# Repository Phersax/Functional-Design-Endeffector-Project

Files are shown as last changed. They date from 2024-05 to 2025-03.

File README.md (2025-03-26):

# Robotic Grippers Comparative Analysis  




## Project Overview  
This study aims to conduct a comparative analysis between two types of grippers used in robotic manipulation: a 3-finger parallel gripper and a 3-finger adaptive gripper. The research will begin with a description of the development of the parallel gripper and will continue with the design of an adaptive phalanx that will convert the developed parallel gripper into an adaptive gripper. Additionally, the analysis will include a thorough evaluation of the performance of both devices, with particular emphasis on their manipulation capabilities.
The 3D modeling will be carried out using SolidWorks software.

Open-source comparison of two robotic gripper designs:  
- 3-Finger Parallel Gripper  
- 3-Finger Adaptive Gripper (convertible from parallel version)  

Designed for academic research and DIY robotics enthusiasts.  

## Assembly
<p align="center">
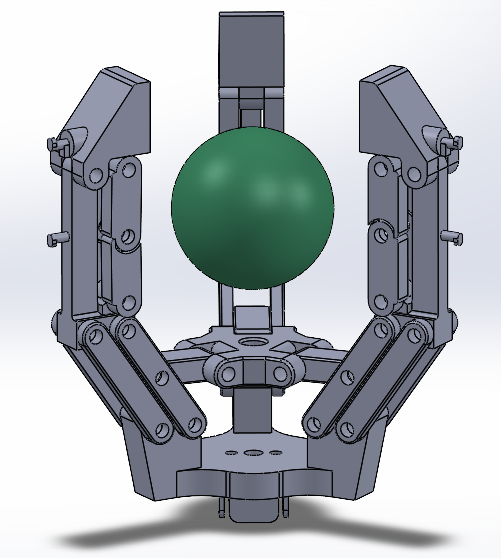
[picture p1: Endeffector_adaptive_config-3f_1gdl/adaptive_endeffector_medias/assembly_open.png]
  
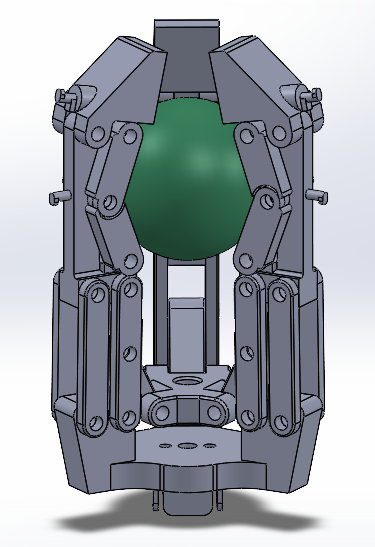
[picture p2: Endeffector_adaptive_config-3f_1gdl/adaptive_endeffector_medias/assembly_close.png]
  
</p>

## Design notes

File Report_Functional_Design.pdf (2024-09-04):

## POLITECNICO DI BARI

DIPARTIMENTO DI INGEGNERIA ELETTRICA E DELL’INFORMAZIONE

LAUREA MAGISTRALE IN INGEGNERIA DELL’AUTOMAZIONE

## Applied Mechanics - Functional Design

## Prof. Ing. Massimo Maria Foglia

# Title:

## Transition from Parallel Gripper to Adaptive Gripper: Design and 3D Simulations

## Students: Francesco Di Chio Nicola Saltarelli Francesco Stasi

ANNO ACCADEMICO 2023-2024

Abstract

This study aims to conduct a comparative analysis between two types of grippers used in robotic manipulation: a 3-finger parallel gripper and a 3-finger adaptive gripper. The research will begin with a description of the development of the parallel gripper and will continue with the design of an adaptive phalanx that will convert the developed parallel gripper into an adaptive gripper. Additionally, the analysis will include a thorough evaluation of the performance of both devices, with particular emphasis on their manipulation capabilities.
Through a series of experimental tests, the performance of the two grippers will be examined in different operational contexts to provide a detailed analysis of their features and advantages. The objective is to provide an in-depth understanding of the performance differences between the two devices.
The 3D modeling will be carried out using SolidWorks software. This process will be documented in the report to ensure a clear understanding of the model development process and the methodologies employed.

CONTENTS

## Contents

Introduction | 1
1 Robotic grippers | 2
2 Parallel gripper design | 6
3 Adaptive finger design | 15
4 Experimental Results | 20
Conclusion | 28
References | 29

CONTENTS

## Introduction

Human labour has always been associated with the acquisition of specific skills, methods, and tools making the work and its environment easier and more effective. Increasing competition from industrial robots for tasks normally carried out by human hands has led to the need for more effective handling equipment, especially prehension tools (more commonly called “grippers”). However, industrial robots are not simply a substitute for people. Their relevance is more often in applications beyond the normal ability (physical or temporal) of conventional manpower. Examples include dirty, hazardous and repetitive work. Just as human hands are the organs of human manipulation, so are robot grippers usually the only parts in direct contact with the workpiece.

Among the wide types of end-effectors, grippers are largely used thanks to their relative simplicity and efficiency in part-handling applications and grasping any physical object, according to the design of the gripper, that can be also manipulated by human hands.

These are the main reasons behind the project, focused on the complete design of two grippers. Starting from the parallel configuration, an adaptive gripper based on the parallel one will be implemented, showing the process of switching from one configuration to another and benefits.

The paper shows all the most important characteristics and steps done in order to develop the grippers.
After a brief introduction and the various classifications that can be made on the robotic grippers, the parallel gripper’s design process will be presented, showing the base mechanism of the gripper, the fingers displacement and the degree of freedom analysis and the design of all parts of the gripper, realized using the SolidWorks software.
The report therefore focuses on the transition to adaptive configuration, showing the new custom parts developed and the main choices made regarding the DC motor and the linear springs to be used.
These choices are important because they have a very close consequence on the operation of the gripper and on the simulation and experimental results obtained in SolidWorks, on which the successive part of the report is focused.
The last part of the papers aims to analyse the results from the SolidWorks simulations, showing advantages and disadvantages of using the two different configurations in terms of applied forces variations, adaptability and forces distribution.

1 ROBOTIC GRIPPERS

## 1 Robotic grippers

A robotic gripper is an essential component of a robotic manipulator. It serves as the robot’s hand and allows the robot to manipulate objects. Recently robotic gripper is widely used for different tasks in various fields. Variety of robotic grippers is developed in high flexibility and multi-function. This project is aimed to study current existing robotic grippers, focusing on the distinction between adaptive grippers and parallel grippers, using a model with three fingers and two phalanges.

### 1.1 Classification

The wide range of shape, size and weight of objects to be manipulated in a production process led to designing of a various types of grippers, that has to be properly selected for a specific task. Therefore is important to distinguish and knowing the grippers types in order to do the correct choice when needed.

### 1.1.1 Configuration-based classification

According to their configuration, grippers can be distinguished in terms of:

- number of fingers : the base configuration of a gripper needs two fingers, sufficient to do the majority of production and manipulating tasks, such as assembly or pick and place. By incrementing the number of fingers one can achieve configurations with multiple fingers for more accuracy and precision in grasping sensitive and fragile objects.

Figure 1: Adaptive three-fingered gripper.

- shape of gripper : grain-filled flexible ball grippers and bellow grippers works changing the shape of the end effector in real time changing the amount of air in the balloon that, in this case, rappresents the gripper. These grippers are also called “Air-Hand” grippers.

### 1.1.2 Actuation-based classification

From the actuation point of view, grippers can be divided in terms of:

- Mechanical actuation : mechanical fingers, that are integral part of the mechanism, are actuated by the main mechanism to grasp objects.
- Cable-driven or sensory feedback actuation : This type of gripper is equipped with a lot of sensors for control purposes. In this type of gripper the design of the robotic arm and the end effector has to be done in order to match with wiring requirements.
- Vacuum grippers : the high level of flexibility of this gripper, while providing a good grip of an object, is due to the use of a rubber or foam suction part to hold the object.

1 ROBOTIC GRIPPERS

Figure 2: Mechanical gripper.

- Hydraulic actuation : using hydraulic pumps one can produce more grasping force compared to other actuations. The disadvantage of hydraulic grippers is that they need constant maintenance.
- Pneumatic actuation : the fingers movement and displacement is made by changing the air pressure in the valve. Small dimensions and low weight are key factors to pay attention to when this type of gripper is used.
- Servo-electric actuation : Using servo-motors used to control the fingers ensures high flexibility and low maintenance costs.
- Magnetic actuation : Making use of the principles of magnetism, these are used for holding ferrous objects.

### 1.1.3 Stiffness-based classification

This important classification in based on the material’s stiffness. In particular the main division is relative to:

- Rigid grippers : these are the traditional ones and they are largely used in industrial applications, in which high precision and less flexibility of fingers is required.
- Soft grippers : the fingers are made by flexible material, allowing to grasp object with very different shapes. These types of grippers and robots are currently important areas of interest for scientists and engineers, especially for medical applications. Grain-filled flexible ball grippers and bellow grippers belongs to soft robots, such as the universal grippers.

Figure 3: Soft gripper.

1 ROBOTIC GRIPPERS

### 1.1.4 Application-based classification

Grippers are not only used in industrial applications, but they also works in:

- Surgical application : especially for Minimally Invasive Surgery (MIS), small grippers and soft grippers are the main choice.
- Assistive application : there are a lot of grippers designed for people with disabilities or, for example, mounted on Unmanned Aerial Vehicle (UAV).
- Research application : a big area of interest is also linked to underwater or underground researches.

### 1.2 Case study

As previously mentioned, the primary objective of this study is to conduct a comparison between parallel and adaptive grippers. Therefore, this subsection will outline the main differences between these two types of devices to facilitate understanding of the results obtained from this research.

### 1.2.1 Parallel grippers

Due to their simplicity of control and relatively low cost, parallel grippers have been widely utilized as end-effectors in industrial robotic systems. Particularly, parallel grippers with fingers moving along a single linear trajectory are notably easy to use. This is because the position of both fingers relative to the linear trajectory remains consistent and constant throughout. This feature greatly simplifies the control process and ensures precise repeatability of operations.

Figure 4: Gripper with linear guide mechanism (Kobayashi et al., 2019).

The collision free space of the motion of the robot which the gripper is attached to depends on the dimensions of the gripper. When grasping objects with different dimensions is performed using a single gripper, the width of the gripper is determined by the largest dimension of the objects; on the other hand, a gripper with large width is undesirable from the collision free space of the robot motion point of view. Because of this issue, the parallel grippers have been usually utilized for tasks to handle the same or a similar dimensions of objects, not for tasks to handle of objects with different dimensions. Grasping of the same or a similar dimensions of objects can be realized by a compact gripper with a compact linear guide mechanism having short stroke.
(Kobayashi et al., 2019) [4] addresses the issue of parallel grippers using the linear guide mechanism and proposes a new parallel open-close gripper.
The width of the proposed gripper depends on the fingers opening width, that is, the gripper becomes small when it grasps a small object and becomes large when it grasps a large object. The proposed gripper can be applied to tasks handling objects with different dimensions without restricting the collision free motion space.

1 ROBOTIC GRIPPERS

Figure 5: Gripper with parallel four bar mechanism (Kobayashi et al., 2019).

With this mechanism, the gripper can open and close fingers with keeping their orientations constant. Normally, the grasping flat surfaces of fingers are parallel to each other. The width of the gripper with four bar parallel linkage can be designed smaller than its finger stroke.

### 1.2.2 Adaptive grippers

An adaptive mechanical system is one in which some form of intelligence is embedded into the mechanics. In such a system, no sensors or complex controllers are required to perform the main task since the mechanical system itself will provide the required adaptive behavior.
In many robotic applications, the manipulation of objects with very complex mechanical hands is not essential and grasping devices are sufficient. However, simple grippers are not appropriate in most cases because they are not capable of adapting to the shape of different objects.
Hence, the development of versatile robotic hands which are capable of grasping a wide variety of objects with a very simple control structure is of great interest for many applications.
It is clear that robot hands based on the latter principle are adaptive mechanical systems since they can adapt to the shape of the objects simply by the mechanical action of their components. Since this behaviour implies that motion takes place without control actions, underactuation must be introduced.
An underactuated mechanism is one which has fewer actuators than degrees of freedom (dof)s. When applied to mechanical fingers, the concept of underactuation leads to mechanical adaptiveness. Mechanically adaptive fingers envelope the objects to be grasped and automatically adapt to their shape with a limited number of actuators usually one and without complex control strategies. The implementation methods of underactuated mechanisms are generally classified into three types: using tendon [6], linkage mechanism [7], and mechanical elements such as gears [8].Most of the research of the underactuated mechanism is focusing on reducing the control complexity of multi fingered robot hands.

2 PARALLEL GRIPPER DESIGN

## 2 Parallel gripper design

The proposed gripper consists, as shown in the Figure 6, of three identical fingers equally spaced along a circumference, dividing it into three equal parts. The fingers displacement is realized thanks to a quite simple mechanism driven by a single actuator : a small DC motor, having its own screw shaft, moves in a linear way the gripper’s palm connected to it and, thanks to a rods system, this displacement generates the opening and closing fingers’ movement.

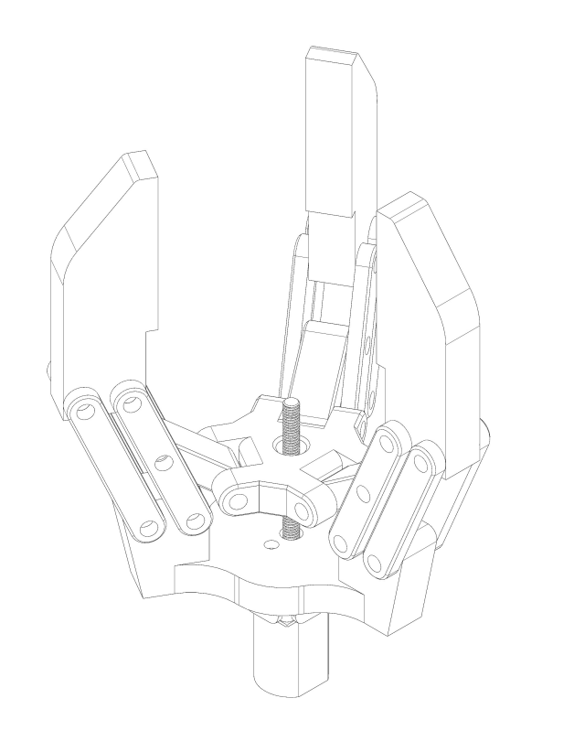
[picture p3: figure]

Figure 6: Model of the three fingers parallel gripper

The proposed solution is especially suitable for the grip of spherical or cylindrical objects, on which the grip is firm and the pressure applied is uniform thanks to the three contact points.
The main advantages that characterize the gripper are in terms of efficiency, ease of implementation and costs thanks to the reduced number of parts.

### 2.1 Degree of freedom analysis

Focusing on a single finger, one can demonstrate that the mechanism allowing the movement is characterized by one degree of freedom. This is an important feature, because it allows a fairly simple study of the kinematic behavior of the entire gripper.

In order to demonstrate this, the Grübler’s formula can be used, which states the number of degrees

2 PARALLEL GRIPPER DESIGN

of freedom of a mechanism can be calculated in the following way:

dof = m(N − 1 − J) +X

J

i=1

fi | (1)

where:

- dof : degrees of freedom of the mechanism;
- m : equal to 6 for spatial bodies, 3 for planar;
- N : number of bodies, including ground;
- J : number of joints;
- f : degrees of freedom of each joint.

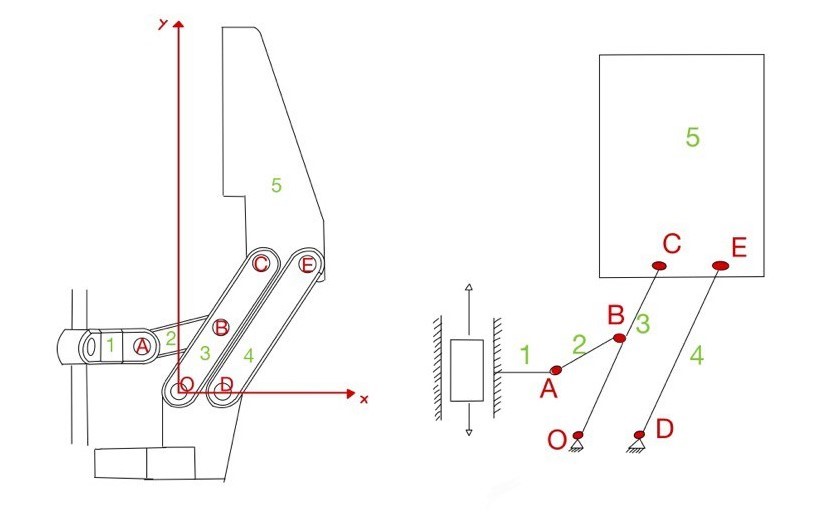
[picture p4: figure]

Figure 7: Constraints analysis

According to the Figure 7, one can see that every finger mechanism is characterized by five bodies (six with the ground), six revolute joints (A,B,C,D,E,O) and one prismatic joint to which the body 1 is subject. In addition, the movement of each finger can be seen as a planar motion.
For this reasons one can stated that m is equal to 3, N is equal 6, J is equal to 7 and the and the sum value is equal to 7 because for every joint there is one degree of freedom.
Applying this values to the Grübler formula one can have:

dof = m(N − 1 − J) +X

J

i=1

fi = 3(6 − 1 − 7) + 7 = 1 | (2)

2 PARALLEL GRIPPER DESIGN

### 2.2 Finger displacement analysis

The chosen approach for studying the kinematic behavior of the finger mechanism makes use of the complex numbers in order to generate the so called closing equation in 2D. Following this method, the mechanism is outlined through vectors expressed as complex numbers, so in terms of magnitude and phase. Using the Euler formula, a non linear system of equations can be obtained and its resolution allows to have a general understanding of the possible displacement of the mechanism.

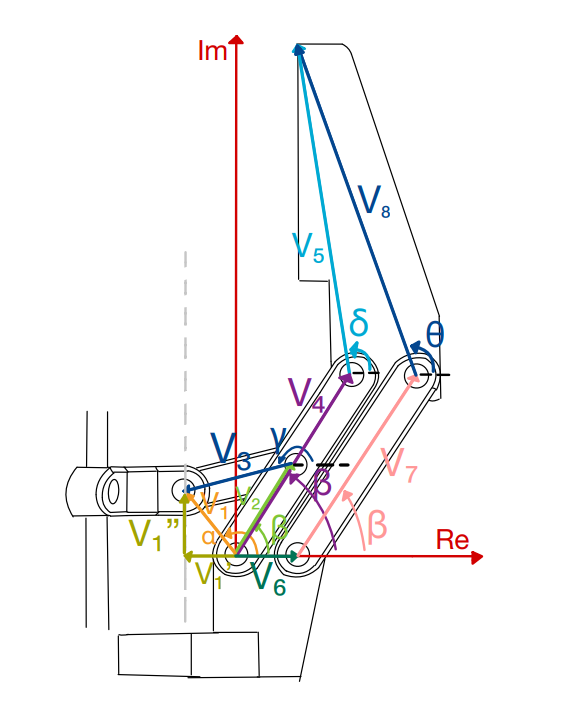
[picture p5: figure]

Figure 8: : Closed kinematic chains

In order to study the mechanism two closing equations have been developed. The first one states that:

V1 − V2 − V3 = 0 | (3)

Expressing the vector V1 as sum of V

′
1

and V

′′
1

the final closing equation is:

V

′
1 + V

′′
1 − V2 − V3 = 0 | (4)

Expressing the equation (4) in terms of amplitude and phase one can obtain :

V

′
1

e

−jπ + V

′′
1

e

j

π
2 − V2e

jβ − V3e
jγ = 0 | (5)

2 PARALLEL GRIPPER DESIGN

Using the Euler formula e

jx = cos(x) + jsin(x) , one can divide the closing equation into two equations, one for the real part and one for the imaginary one. In this way one can obtain a non linear system of two equations in two unknowns, that in this case are the angles β and γ.

The feasible range of variation of V

′′
1 was experimentally deducted from SOLIDWORKS. The range of variation used in Matlab for the non linear system resolution is therefore:

V

′′
1 = [−1.79 : 11.2] | (6)

expressed in mm and referred to the origin.

The same method was used also for the second closing equation :

V4 + V5 − V6 − V7 − V8 = 0 | (7)

Expressing the equation (7) in terms of amplitude and phase one can obtain:

V4e

jβ + V5e

jδ = V6e
j0 + V7e

jβ + V8e
jθ | (8)

After simplifications and using the Euler formula you obtain another non linear system of two equations.

The obtained results are shown in the following figures :

Figure 9: Initial position of the mechanism

2 PARALLEL GRIPPER DESIGN

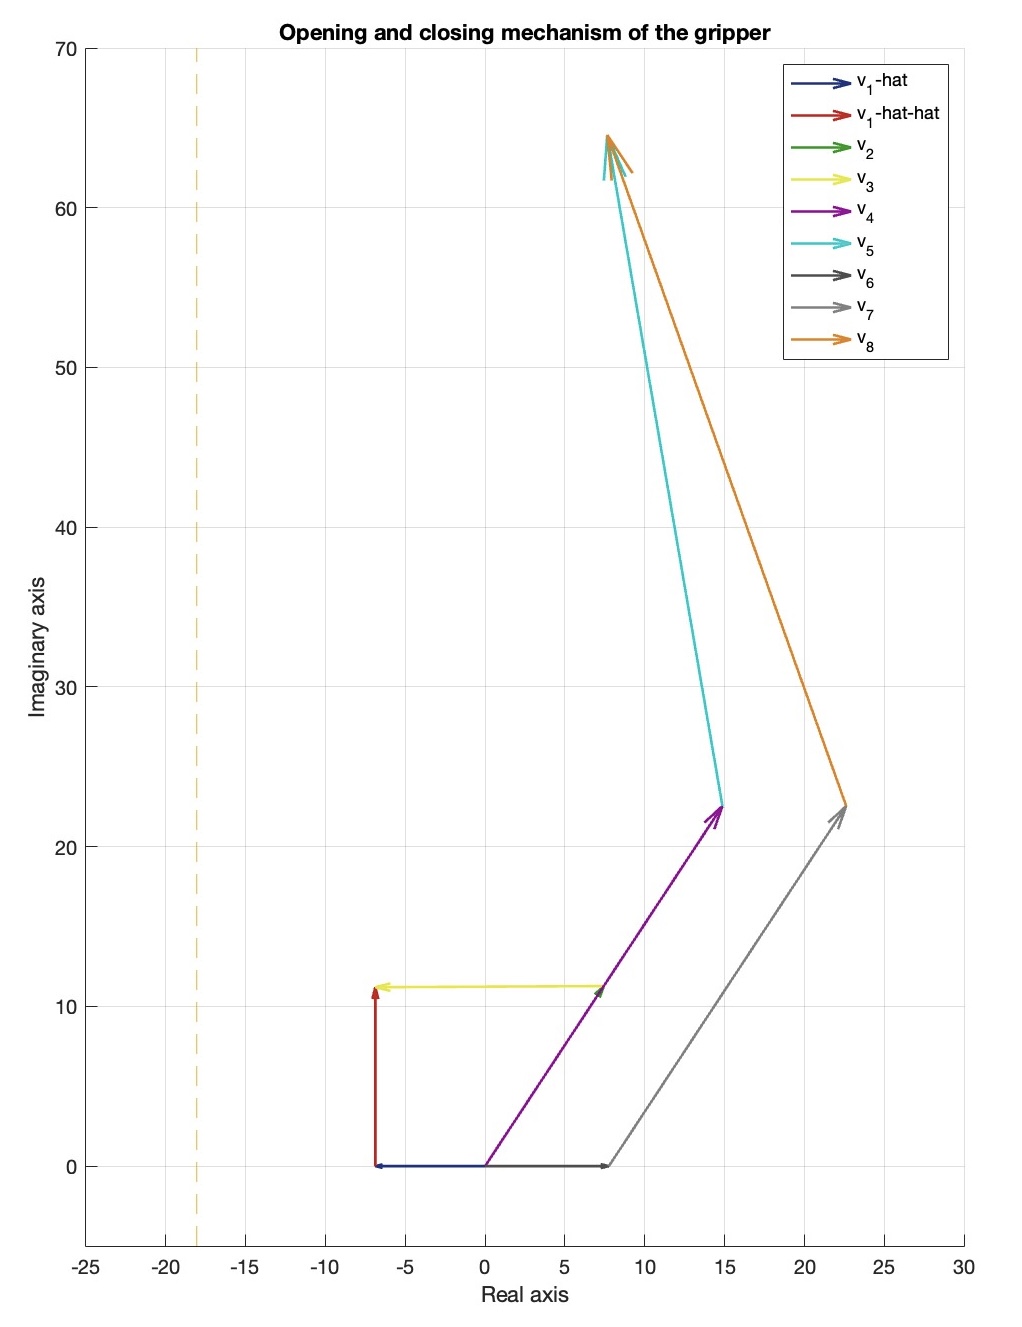
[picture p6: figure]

Figure 10: Final position of the mechanism

### 2.3 SolidWorks 3D model

The 3D model of the designed gripper was developed using SolidWorks, a very powerful software useful also for the contact forces analysis.
The design process started with the creation of fully customized individual parts which were later assembled thought concentricity and coincidence constraints, thus generating the final model.

### 2.3.1 Base part design

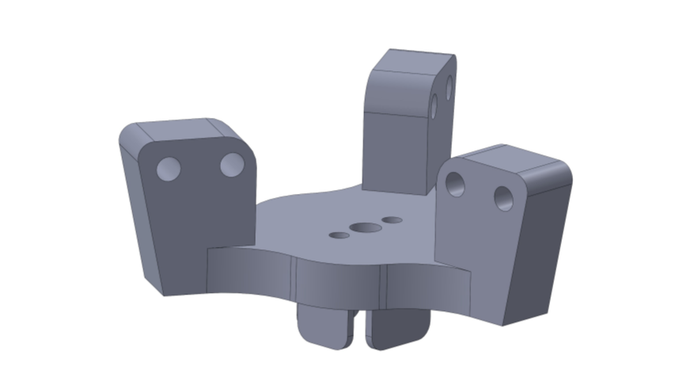
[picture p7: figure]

Figure 11: Base part design

2 PARALLEL GRIPPER DESIGN

The base is mainly composed of a flat main extrusion and three external along the circumference on which there are holes for the connecting rods between the base and the finger. The base is also provided by a central holes and an adapter in the lower part to accommodate the motor and the shaft.

### 2.3.2 DC motor enclosure

The chosen actuator is the 12 GA Miniature DC Gear Motor Screw Shaft. The developed casing ensures a good protection against external agents, increasing the reliability of the gripper.

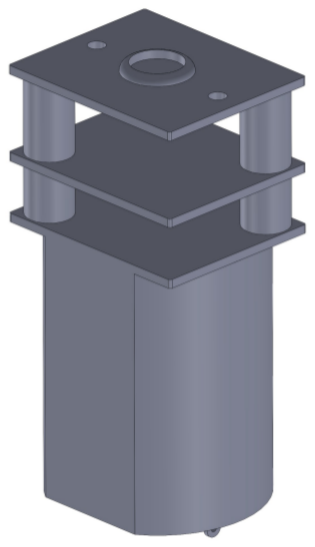
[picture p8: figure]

Figure 12: DC motor enclosure

### 2.3.3 Threaded shaft design

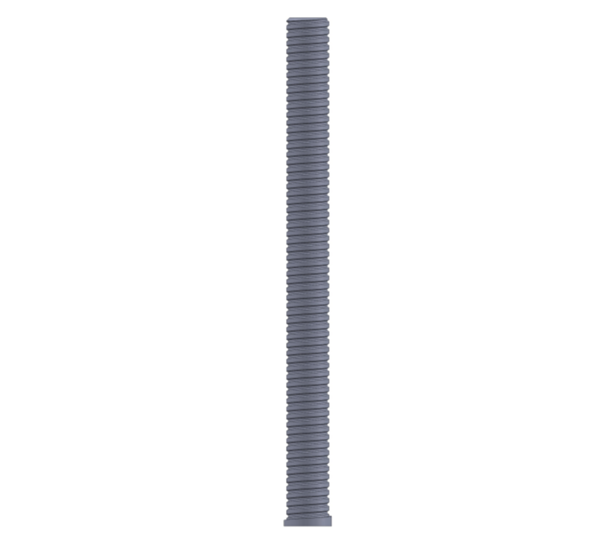
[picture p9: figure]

Figure 13: Threaded shaft

2 PARALLEL GRIPPER DESIGN

The opening and closing fingers movement is possible thanks to a threaded shaft, to which the palm of the gripper is attached, moved by the DC motor. The construction parameters of the shaft are height (32 mm) and pitch (0.5 mm).

### 2.3.4 Palm design

The central element of the gripper mechanism is the fully customized palm. The central hole accommodate the DC motor shaft, while the six external holes generate the revolute joints connecting the palm with the rods.
The design of the palm required much attention in order to have a contact-free slide between the palm and all other parts of the gripper, especially with the base.

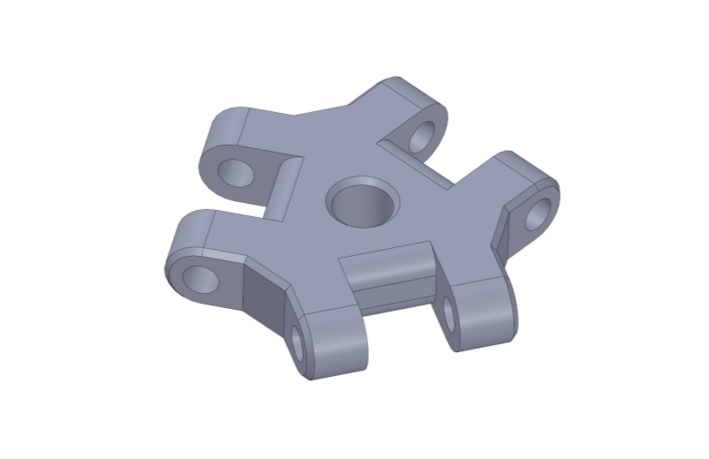
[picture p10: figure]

Figure 14: Gripper palm

### 2.3.5 Connection rods

Three types of rods are used in order to realize the opening and closing finger movement.

The first type of rods makes possible the connection between the base and the finger. In particular, these rods have two holes : one creates the revolute joint with the external hole of the external extrusion of the base, while the second hole generates the external revolute joint on the finger.

The second type of rods is characterized by the same dimensions of the first type rods, but with an additional central hole. The two external holes have the same function of the first type rods ones, while the central one makes the connection with the third type rods.

The third type rods are are shorter and thicker with respect to the other types rods. These rods create a connection between the palm and the central hole’s second type rods.

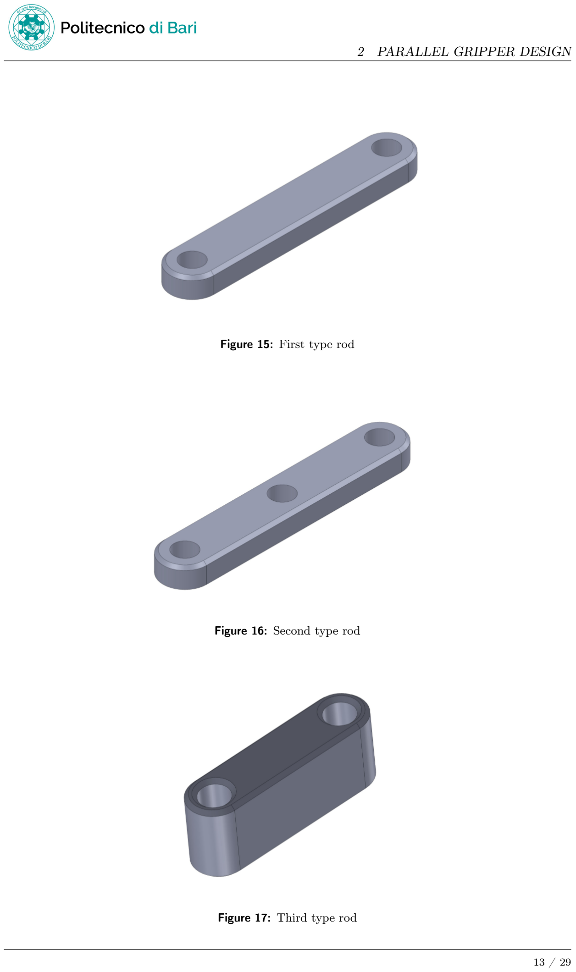
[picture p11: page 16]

2 PARALLEL GRIPPER DESIGN

Figure 15: First type rod

Figure 16: Second type rod

Figure 17: Third type rod

2 PARALLEL GRIPPER DESIGN

### 2.3.6 Finger design

The finger is quite simple single part, obtained with a simple extrusion. You can notice that that flat internal part make contact with the object to be grasped. The flat design allows to grasp spherical object with different size a very solid way.
The holes realize the revolute joint with the first and second type rods.

Figure 18: Gripper finger

3 ADAPTIVE FINGER DESIGN

## 3 Adaptive finger design

To enable the transition from a parallel gripper to an adaptive one, a specific modification was made to the non-adaptive phalanx, avoiding alterations to the entire model. This strategy allowed us to obtain an adaptive gripper simply by modifying the final phalanx of the parallel gripper, while keeping the palm and the opening and closing mechanism unchanged. This approach was chosen with the objective of comparing the two models, as described in the project abstract.

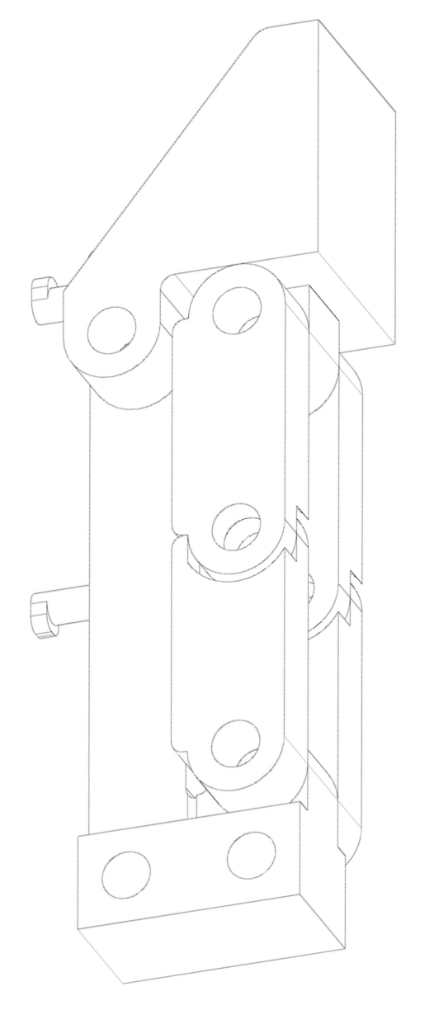
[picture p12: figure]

Figure 19: Adaptive finger’s sketch

For simplicity, in this section we will focus exclusively on describing the adaptive phalanx model of the gripper, as it would be redundant to describe again the base and palm of the gripper. Thanks to this adaptive phalanx, it is now possible to grasp objects by adapting the phalanx to the shape of the object. All of this is made possible through the use of springs.

When the phalanx comes into contact with an object, the four front segments, as depicted in Figure 19, move and conform to the surface of the object, enabling a secure and flexible grip. The springs assist in restoring the phalanx to its original position once the object is released, ensuring that the phalanx always returns to its initial configuration, ready for the next gripping operation.

Utilizing an adaptive phalanx offers numerous advantages:

- Greater Flexibility: The ability to adapt to various shapes and sizes of objects makes the gripper highly versatile.
- Secure Grip: Automatic adaptation to the object’s surface enhances grip stability and security, reducing the risk of slippage.

3 ADAPTIVE FINGER DESIGN

- Simplicity of Design: Using springs for restoring the original position is a simple and effective solution that does not require complex control systems or additional actuators.

These advantages make the adaptive gripper an efficient and versatile solution, significantly enhancing the capabilities for grasping and manipulating objects.

### 3.1 Degree of freedom analysis

In this subsection, the degrees of freedom of the adaptive phalanx will be determined, following the method previously used to analyze the opening and closing mechanism of the parallel gripper. This calculation quantifies the number and nature of independent movements that the adaptive phalanx can perform.

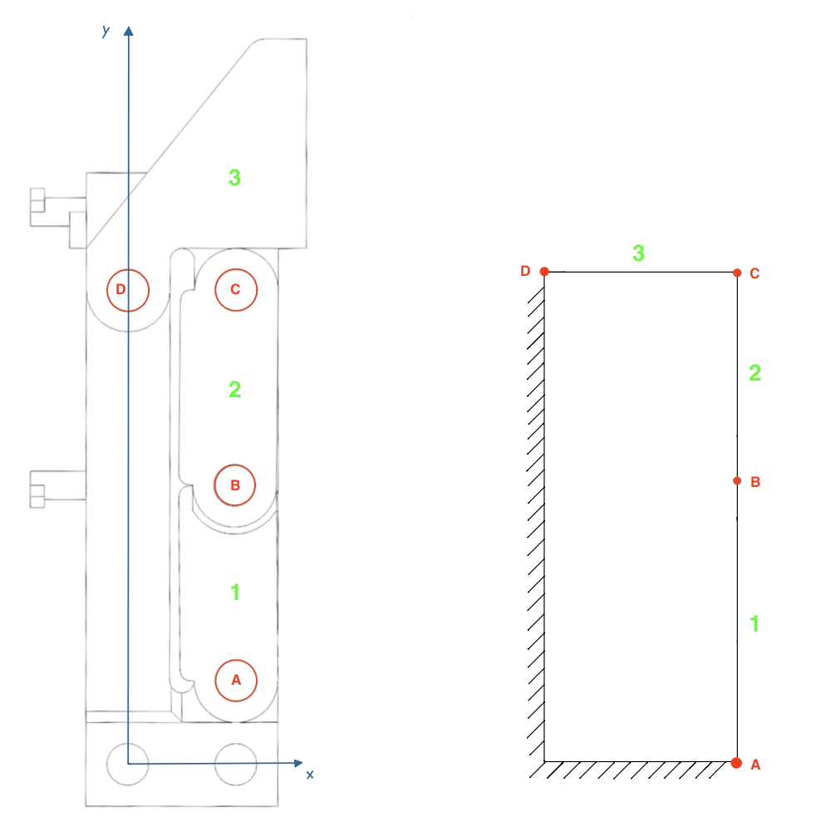
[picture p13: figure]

Figure 20: adaptive finger’s dof analysis

In Figure 20, on the left, a technical side view of the adaptive phalanx is shown, while on the right, a simplified schematic representation facilitates the calculation of its degrees of freedom. The phalanx is equipped with 4 revolute joints and consists of 3 bodies. Therefore, the degrees of freedom of the phalanx are:

dof = m(N − 1 − J) +X

J

i=1

fi = 3(4 − 1 − 4) + 4 = 1 | (9)

3 ADAPTIVE FINGER DESIGN

### 3.2 SolidWorks 3D model

### 3.2.1 Fixed part of the adaptive finger

The fixed part of the adaptive finger in Figure 21 is designed in an L-shape. This part connects the tip of the finger with the bars, which in turn are connected with the base and palm of the end-effector.
The part is designed not to collide with the movable phalanges during closing and opening. A spring attachment is also added, as well as a slide rail (a channel that only allows elongation and compression while preventing it from moving laterally).

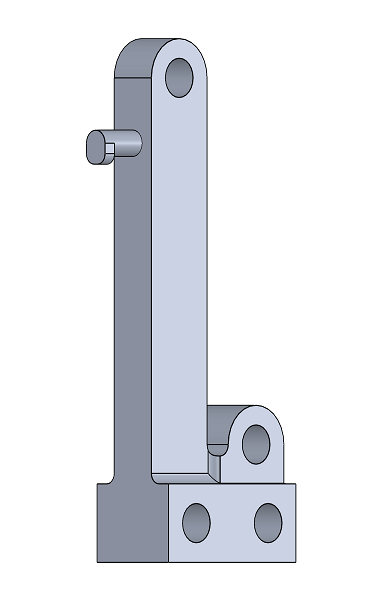
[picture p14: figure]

Figure 21: fixed finger part

### 3.2.2 Mobile phalanges

Phalanges are composed of the same repeated part so that assembly is less complex. In particular, they are made similarly to the connection bars of the static model, but with some tricks to maintain a reduced thickness by modifying the connection between upper and lower phalanges.
In addition, a knocker necessary to prevent reverse rotation of the bars is added. This knocker implies a rotation limitation between the constraints during simulation.
Figure 22 shows the connection between upper and lower phalanges, made with the same repeated part.

3 ADAPTIVE FINGER DESIGN

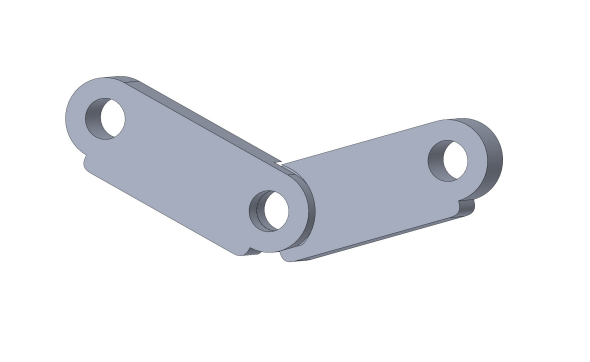
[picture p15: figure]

Figure 22: mobile phalanges parts

### 3.2.3 End part of the finger

The terminal part of the adaptive finger (figure 23) must connect the fixed part with the movable phalanges. Care is taken to avoid creating intersections during movement. The profile is made from the static model of the end-effector. The second hook of the spring is then inserted.

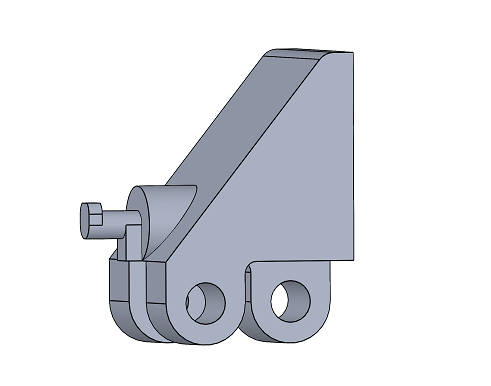
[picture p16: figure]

Figure 23: terminal finger part

3 ADAPTIVE FINGER DESIGN

### 3.2.4 Parts assembly

The finger, which will be directly substituted for the three fingers of the static model, is thus assembled; the spring brings the end-effector to the rest configuration.
Figure 24 shows the finger assembly with a bending test and the addition of the spring for a dynamic study test, while a complete assembly of the new adaptive end-effector can be seen in figure 25.

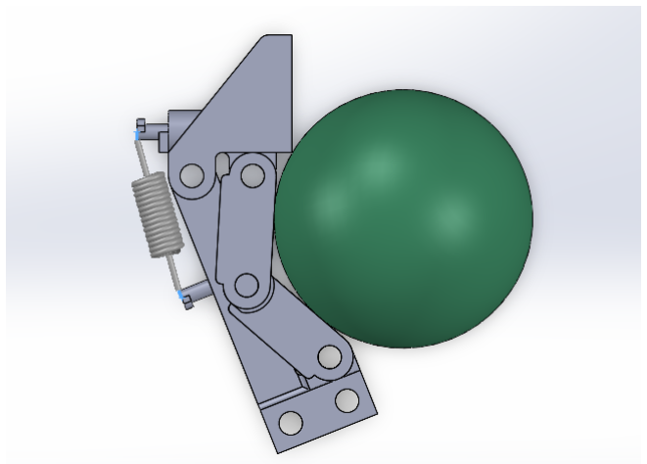
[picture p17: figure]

Figure 24: finger assembly

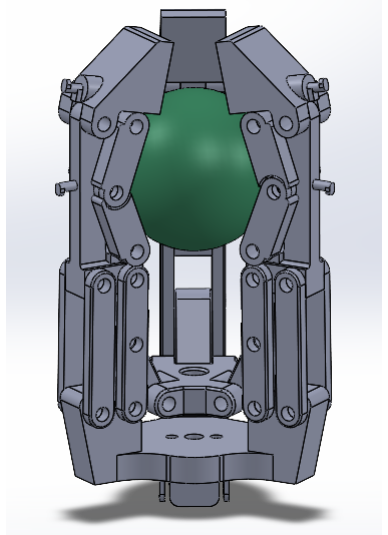
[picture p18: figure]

Figure 25: Complete assembly

4 EXPERIMENTAL RESULTS

## 4 Experimental Results

In this section of the documentation, the results of simulations conducted using Solidworks Motion will be presented. The tests were performed to compare the contact force generated by a gripper in both parallel and adaptive gripper configurations.

The object used for the gripping tests is an aluminum sphere 3.0205 (EN-AW 1200) with a variable diameter. Three spheres of different diameters were employed to analyze how the contact force varies with changes in the diameter and mass of the sphere. Aluminum was selected as the material for the sphere due to its mechanical properties, such as lightness and strength, which make it ideal for simulations aimed at obtaining an accurate and representative response under the given load conditions.
It should be noted that the images presented in this section depict the gripper in a simplified version, excluding the motor and threaded rod necessary for the opening and closing mechanism. In the simulation, the motor’s function, opening and closing the fingers, was replaced by a constant force of 55 N applied to the palm of the gripper, enabling the closing and gripping of the object.

### 4.1 Gripping force calculation

This subsection will demonstrate how to calculate the minimum gripping force required to grasp an object, given the coefficient of friction between the object and the rubber applied to the gripper’s phalanges, as well as the mass of the object itself. The use of rubber pads on the phalanges is particularly beneficial as it enhancing the grip and reducing the risk of the object slipping.

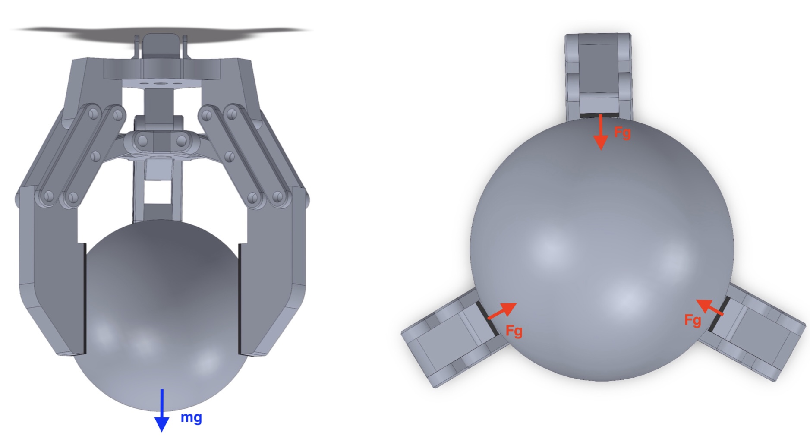
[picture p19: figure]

Figure 26: Parallel gripper in contact with a large sphere.

As shown in Figure 26, the left side displays a front view of the parallel gripper while grasping a sphere, which is the object used for the simulation. On the right side, a bottom view is provided, where the directions of the gripping forces necessary to hold the sphere in place are indicated. Therefore, the gripping force required to grasp the object on each phalange is:

Fg =

mg
µN
∗ S | (10)

4 EXPERIMENTAL RESULTS

where Fg is the gripping force to be applied to each phalange, m is the weight of the object to be grasped, g is the gravitational constant, µ is the coefficient of friction between the materials in contact, N is the number of gripper fingers and S is a safety factor, typically set to 2.

### 4.2 Choice of linear spring

As shown in Figure 24, each finger of the adaptive configuration requires a linear spring that allows the finger to adapt correctly to the object to be grasped, also ensuring the return to the vertical position of the finger when the palm of the gripper is fully raised.
For these reasons the choice of the spring to be used is extremely important, having important consequences for the behaviour and functionality of the gripper.

The chosen spring is a cheaper one, easily available and purchasable on the web, shown in the Figure 27 :

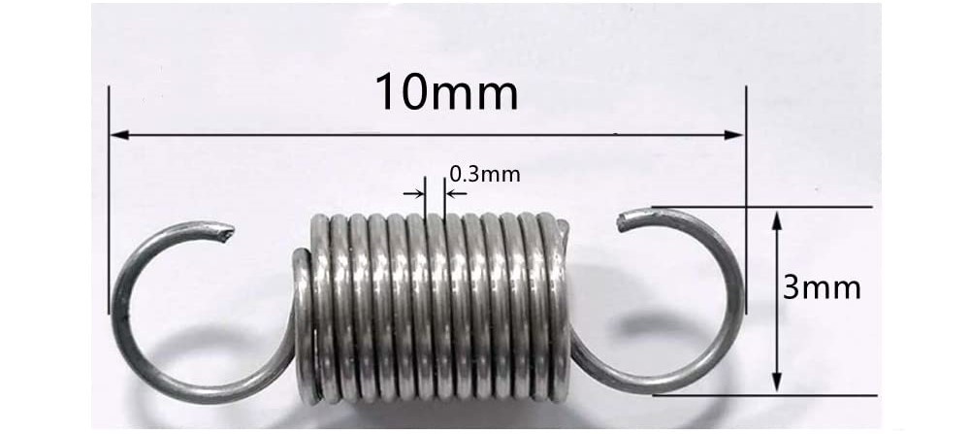
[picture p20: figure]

Figure 27: Linear spring’s parameters

In order to carry out the simulations on Solidworks Motion, the elastic constant and the free length of the spring have to be known.
The free length can be derived from the Figure 27 (10 mm), while the elastic constant is not provided, so is necessary to calculate it.
In order to do it, the following equation [9] can be used :

k =

Gd⁴
8nD³

(11)

where :

- G is the spring material stiffness module ;
- d is diameter of the spring wire ;
- n is the number of active coils ;
- D is the average diameter of the spring.

By taking these parameters from Figure 27 and setting G = 79 GP a, a typical G-value for steel, you obtain, using the Formula 11, that the elastic constant of the spring is equal to 2.9 N/mm.

This result is acceptable and shows that the spring has a good elasticity. As consequence of this, the finger is characterized by a good adaptability to the objects to be grasped, regardless from the

4 EXPERIMENTAL RESULTS

object size. In addition, if the spring constant is too high, the finger will not be able to bend, thus losing its adaptive behaviour.
Summing up, the great adaptability that can be achieved and the availability of the spring makes make this choice in line with the project’s objectives.

### 4.3 Choice of electric DC motor

The choice of motor is crucial since it determines the maximum gripping force applicable by the endeffector and also the closing and opening speed. Among the various types, the DC motor is chosen, which, having a linear torque characteristic, makes it easy to deduce the force that can be obtained from the feed-forward construction parameters, as shown below:

T = K · ϕ · Ia | (12)

The obtained torque T thus depends only on a constant K given by the construction parameters, magnetic flux ϕ and armature current Ia.

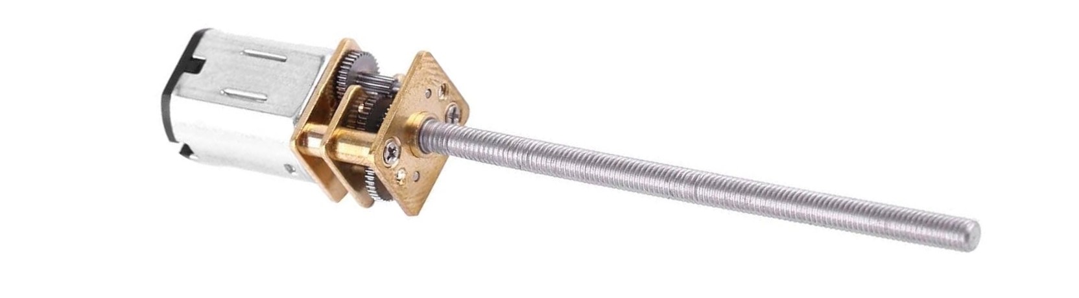
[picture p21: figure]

Figure 28: motor with gearbox

This DC motor must also respect the small size of the system while maintaining a torque capable of making the system functional, even introducing a gearbox to have the right compromise between torque and speed obtained. It is also necessary to transform the rotary motion of our motor into a linear motion suitable for the movement of the palm in our endeffector.
We therefore choose the type of motor shown in Figure 12 that meets the following characteristics, where the M3 threaded rod ensures linear motion.

Then we go on to choose the gearbox to calculate the force of our motor on the palm. Looking at the datasheets of these motors gives indicative tables.
We choose a supply voltage of 6V, with a gearbox that allows a torque at rated load of 4, 903 · 10⁻³Nm and a speed of 100, 531rad/s.
Considering these data, the force transmitted to the palm through the threaded rod can be calculated by the following formula [10]:

F =

2 · π · T · η
P

≈

2 · π · 4, 90 · 10⁻³
- 0.9
0.5 · 10⁻³
≈ 55N | (13)

where :

- F is the resultant force placed on the palm of the endeffector ;
- T is the torque produced by the motor ;
- η is the efficiency set to 0.9 ;
- P is the pitch of the threaded rod equal to 0.5mm for a diameter of 3mm.

4 EXPERIMENTAL RESULTS

In this formula we take into account an efficiency set by us and neglect the friction produced in the movement, however, the value obtained is only indicative of a force that can be used in the simulation phase, this value in fact will always be modifiable by going to check the power parameters of the motor.
To calculate the linear velocity of the palm displacement we can use the following formula where ω is the angular velocity and p is the pitch of the threaded rod. Knowing that the excursion made by the part we can calculate the time taken for the complete opening and closing of the endeffector.
v = ω · p ≈ 50 · 10⁻³mm/s | (14)

### 4.4 Simulations with Large Sphere

In this subsection, the results obtained from the simulation of the parallel and adaptive gripper interacting with a sphere of 26mm radius and approximately 200 g mass will be presented.

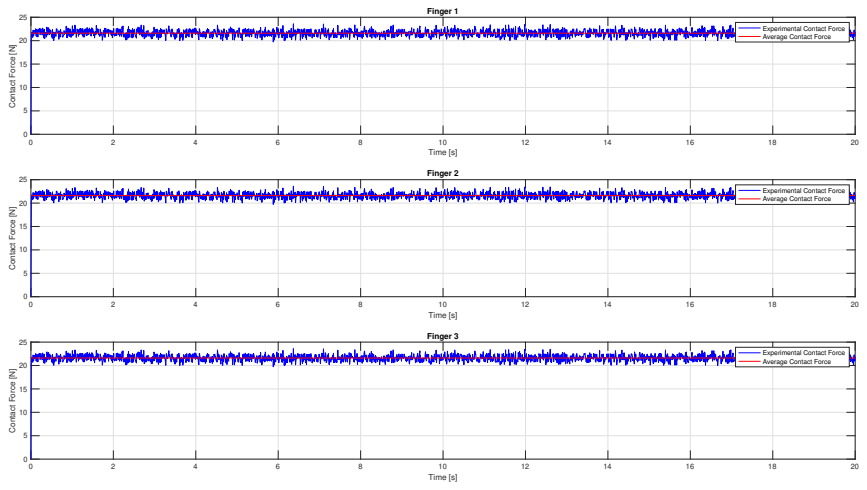
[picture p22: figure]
Time [s]; Contact Force [N]; Finger 1; Experimental Contact Force Average Contact Force; Finger 2; Finger 3

Figure 29: Contact force between the phalanges of the parallel gripper and the sphere.

Figure 29 illustrates the variation in contact force between the phalanges of the parallel gripper and the sphere. It can be observed that the contact force is approximately 22 N, which is higher than the gripping force required to hold the object. Specifically, an aluminum sphere 3.0205 (EN-AW 1200) with a radius of 26 mm has a weight of about 200 g. Given that the static friction coefficient between rubber and aluminum is 0.25, applying Formula 10 yields a gripping force of approximately 5.5 N.

Figure 30 shows the trend of the contact force between the phalanges of the adaptive gripper and the sphere. The graphs highlight that two phalanges per finger come into contact with the sphere. The ’lower phalanx’ refers to the phalanx closest to the palm, while the ’upper phalanx’ is the one situated between the lower phalanx and the outermost phalanx, which is the third and final phalanx of the adaptive finger. It can be observed that once the gripper grasps the object, the contact force is approximately 3.5 N for the lower phalanx and 5.5 N for the upper phalanx.

4 EXPERIMENTAL RESULTS

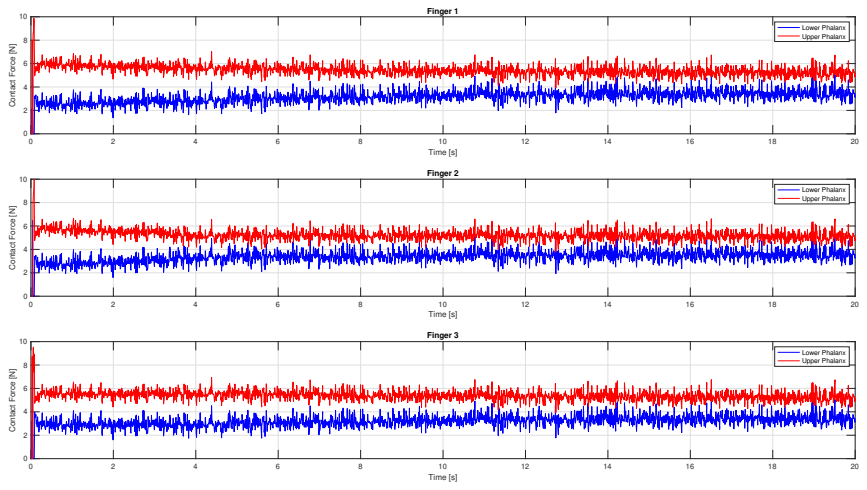
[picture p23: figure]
Time [s]; Contact Force [N]; Finger 1; Lower Phalanx Upper Phalanx; Finger 2; Finger 3

Figure 30: Contact force between the phalanges of the adaptive gripper and the sphere.

### 4.5 Simulations with Medium Sphere

By reducing the size of the sphere to a 22mm radius, we obtain a body with an approximately 120g mass, and we can repeat the previous simulations for the parallel endeffector and the adaptive one.

Figure 31: Contact force between the phalanges of the parallel gripper and the sphere.

Figure 31 shows the simulation results for the parallel endeffector. It can be seen that decreasing the radius also decreases the contact force between phalanx and sphere, specifically the resulting average contact force is about 9 N.
Considering the mass obtained from Solidworks evaluation, and considering Formula 10, we get a gripping force of about 3.15N. So the force exerted is sufficient to grip the chosen object.

4 EXPERIMENTAL RESULTS

Figure 32 shows the contact forces between the upper and lower phalanges with the ball for each of the three fingers. We note that after a transient due to the initial conditions of endeffector position, which allow repositioning of the sphere, steady-state contact forces are achieved.
These forces average less than in the previous case. In particular, a force of about 4N is obtained for the upper phalanx, and slightly more than 2N for the lower phalanx. This difference is due to the consideration of the force of gravity in the simulation, which, by pushing the ball toward the upper phalanges, increases its contact forces.

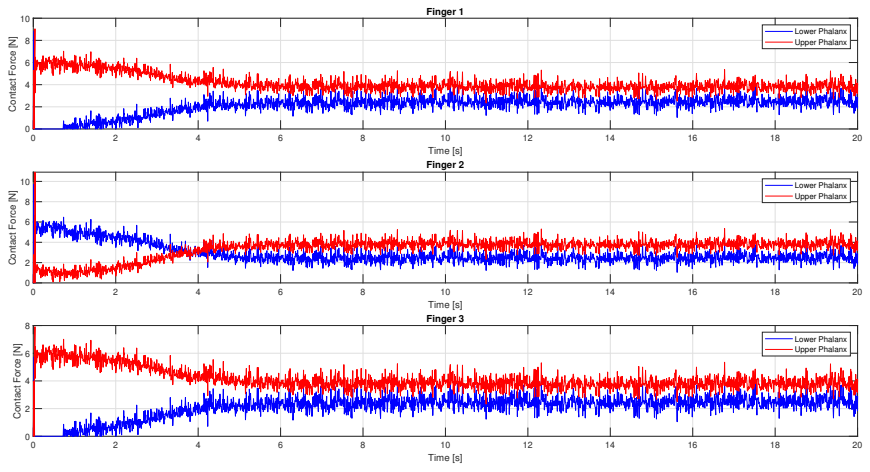
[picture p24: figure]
Time [s]; Contact Force [N]; Finger 1; Lower Phalanx Upper Phalanx; Finger 2; Finger 3

Figure 32: Contact force between the phalanges of the parallel gripper and the sphere.

### 4.6 Simulations with Small Sphere

In order to have a general understanding of the gripper behaviour, simulations with a sphere of 18mm and approximately 60 g have been done, both in parallel and adaptive gripper configuration.

Figure 33 shows the contact force generated between the fingers and the small sphere in case of parallel gripper. It can be observed that the contact force for each finger-sphere contact oscillates around an average value of about 6 N. In particular, the little spikes around the average value are due to the simulation parameters settings in Solidworks.
This result is acceptable according to the Formula 10 which states that, for this specific small sphere aluminium object, the minimum gripping force required is approximately 1.6 N

4 EXPERIMENTAL RESULTS

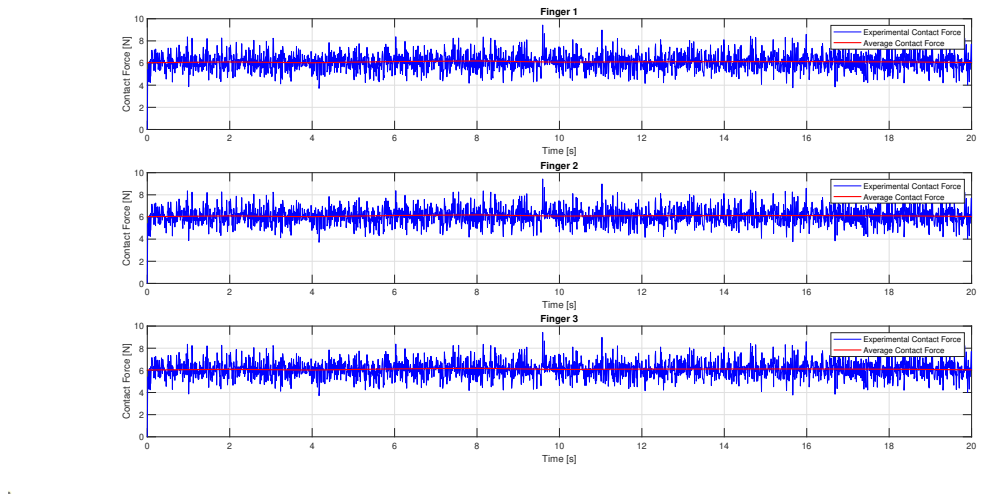
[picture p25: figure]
Time [s]; Contact Force [N]; Finger 1; Experimental Contact Force Average Contact Force; Finger 2; Finger 3

Figure 33: Contact force between the phalanges of the parallel gripper and the small sphere.

Figure 34 shows the trend of the contact forces generated for the fingers-small sphere contact. It should be noted two phases : in the firsts four seconds there is a fingers settling phase which lead the fingers to adapt correctly to the sphere, while in the successive seconds the situation is stable, indicating that the gripper has correctly grasped the ball.
It can observed, focusing on the second phase, that the average contact force is approximately 3 N for upper phalanx and 2 N for the lower one.

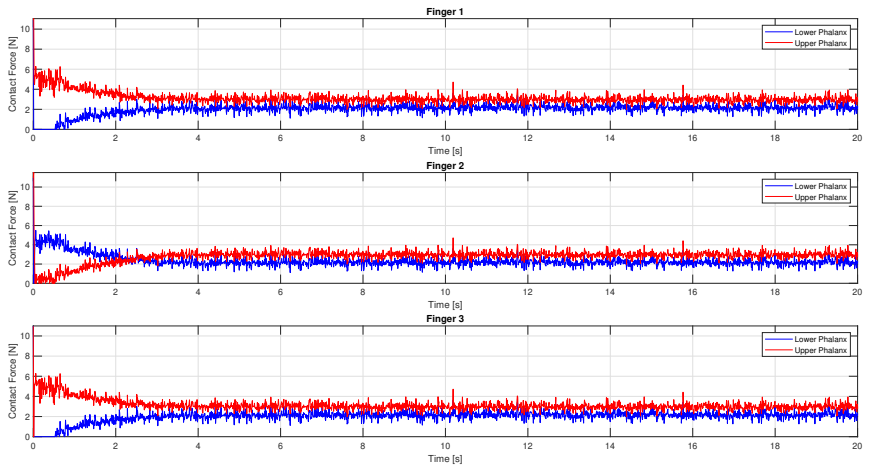
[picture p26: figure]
Time [s]; Contact Force [N]; Finger 1; Lower Phalanx Upper Phalanx; Finger 2; Finger 3

Figure 34: Contact force between the phalanges of the adaptive gripper and the small sphere.

4 EXPERIMENTAL RESULTS

### 4.7 General Conclusions on Contact Force Analysis

Analyzing the contact force charts you may notice some recurring elements both focusing on the graphs relating to the same sphere and by seeing the whole.

From the comparison of the two graphs generated for the same sphere, it can be observed that in the parallel gripper each finger makes contact with the object at a single point, while in the adaptive gripper contact occurs at two distinct points. This characteristic of the adaptive gripper can be considered advantageous, as distributing the contact over multiple points allows for a more uniform and adaptable grip on objects with irregular shapes and surfaces, reducing the risk of damage.

Moreover, it is evident that the contact force between the sphere and the phalanges is, adding all the components, greater in the parallel gripper compared to the adaptive one. This can be explained by the fact that the parallel gripper exerts a concentrated pressure on a single contact point, which can result in a more intense and robust grip. However, this concentration of force may also increase the risk of damaging the object, especially if it is delicate or has an irregular surface. In contrast, the adaptive gripper, with its force distributed over two contact points, tends to apply a more uniform pressure, reducing the risk of damage and improving handling of objects with complex geometries or sensitive surfaces.

In addition, you can notice a general decreasing of the contact force, both in parallel and adaptive gripper configuration, as the size of the sphere decreases. This could be explained, focusing on the parallel gripper configuration and referring to the Figure 7, by the increasing of the linear distance between the point A and the contact point between the finger and the sphere as the dimension of the sphere increases.
In fact, the smaller the sphere is, the closer to the palm will be to the base, increasing that linear distance. Using the principle of levers or moments balance it can be easily seen that the contact force is inversely proportional to the distance between the point A and the contact point, thus confirming the results obtained from the simulations.

4 EXPERIMENTAL RESULTS

## Conclusion

In this study, we conducted a comparative analysis of the performance between a parallel gripper and an adaptive gripper to evaluate their effectiveness in object manipulation. Using SolidWorks, we modeled and simulated both grippers based on an analysis of degrees of freedom and a study of displacements through closure equations. The simulations revealed significant differences between the two configurations.

In summary, parallel grippers offer advantages such as a higher concentrated gripping force, simplified design which reduces production costs, and ease of control and precision due to predictable movement, which minimizes complexity compared to adaptive grippers. On the other hand, adaptive grippers provide uniform force distribution, adaptability to irregularly shaped objects, and a lower risk of damaging delicate items, making them more versatile in handling a variety of objects.

This analysis provides a solid foundation for future development and optimization of grippers, with potential applications across various sectors, from industrial robotics to automated handling in unstructured environments. Future developments for this project include:

- FEM Analysis (Finite Element Method): This phase involves using finite element analysis to simulate material and structural behavior under specific loads. FEM analysis is crucial for optimizing design and predicting the structural performance of the component before physical production.
- 3D Printing: Based on the results of the FEM analysis, 3D printing will be carried out using the same material used in the simulation. This step allows for the production of physical prototypes that reflect the characteristics predicted in the simulation.
- Experimental Validation: Finally, tests will be conducted on the printed grippers to verify the alignment between simulated results and real-world performance. This phase is essential for confirming that the FEM simulations accurately reflect the component’s behavior in practice.

REFERENCES

## References

[1] Gareth J Monkman et al. Robot grippers. John Wiley & Sons, 2007.
[2] Patakota Venkata Prasad Reddy and VVNS Suresh. “A review on importance of universal gripper in industrial robot applications”. In: Int. J. Mech. Eng. Robot. Res 2.2 (2013), pp. 255–264.
[3] Zahra Samadikhoshkho, Kourosh Zareinia, and Farrokh Janabi-Sharifi. “A brief review on robotic grippers classifications”. In: 2019 IEEE Canadian Conference of Electrical and Computer Engineering (CCECE). IEEE. 2019, pp. 1–4.
[4] Akinari Kobayashi et al. “Design and development of compactly folding parallel open-close gripper with wide stroke”. In: 2019 IEEE/RSJ International Conference on Intelligent Robots and Systems (IROS). IEEE. 2019, pp. 2408–2414.
[5] Clément M Gosselin. “Adaptive robotic mechanical systems: A design paradigm”. In: (2006).
[6] Clement Gosselin, Frederic Pelletier, and Thierry Laliberte. “An anthropomorphic underactuated robotic hand with 15 dofs and a single actuator”. In: 2008 IEEE International Conference on Robotics and Automation. 2008, pp. 749–754. doi: 10.1109/ROBOT.2008.4543295. (https://doi.org/10.1109/ROBOT.2008.4543295)
[7] Kuat Telegenov et al. “Preliminary design of a three-finger underactuated adaptive end effector with a breakaway clutch mechanism”. In: Journal of Robotics and Mechatronics 27.5 (2015), pp. 496–503.
[8] Kazuki Mitsui, Ryuta Ozawa, and Toshiyuki Kou. “An under-actuated robotic hand for multiple grasps”. In: 2013 IEEE/RSJ International Conference on Intelligent Robots and Systems. IEEE. 2013, pp. 5475–5480.
[9] Richard G. Budynas and Keith Nisbett. Shigley’s Mechanical Engineering Design. McGraw-Hill, 2011, p. 520.
[10] Richard G. Budynas and J. Keith Nisbett. Shigley’s Mechanical Engineering Design. McGraw-Hill Education, 2020, p. 416.

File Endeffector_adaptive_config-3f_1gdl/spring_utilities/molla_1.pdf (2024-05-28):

### MOLLA A TRAZIONE T31290

Caratteristiche prodotto


Materiale: ACCIAIO AL CARBONIO C85 Do - Diam. Esterno (mm): 4
d - Diametro Filo (mm): 0.8
Lo - Lungh. Libera Int. Occhielli (mm): 12.6 L1 - Mass. Estensione (mm): 15.26
P - Carico a L1 (N): 39.9
T - Tensione Iniziale (N): 5.96
R - Carico Trazione Unitario (N/mm): 12.7

Powered by TCPDF (www.tcpdf.org)

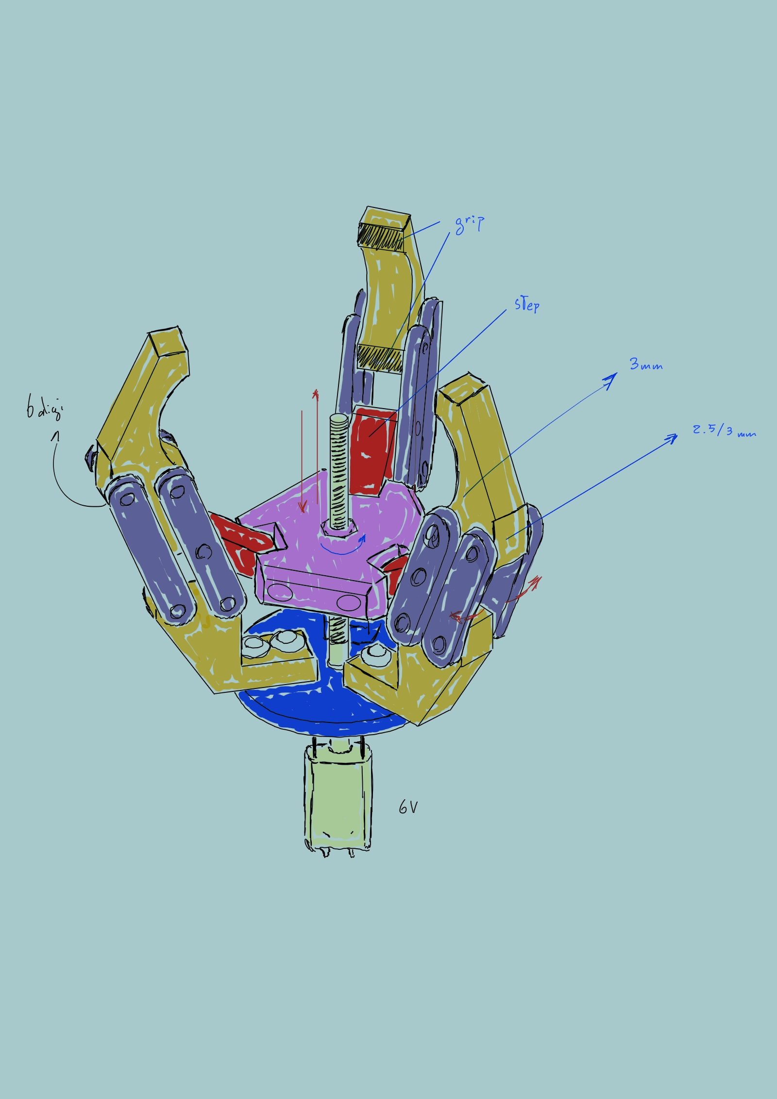
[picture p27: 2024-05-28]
medias/utilities/sketch.jpg

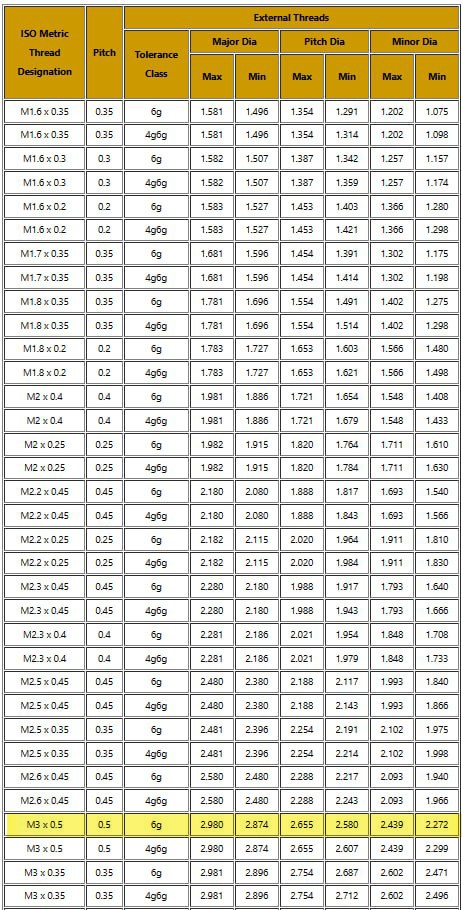
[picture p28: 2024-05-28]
medias/utilities/iso_table.jpg

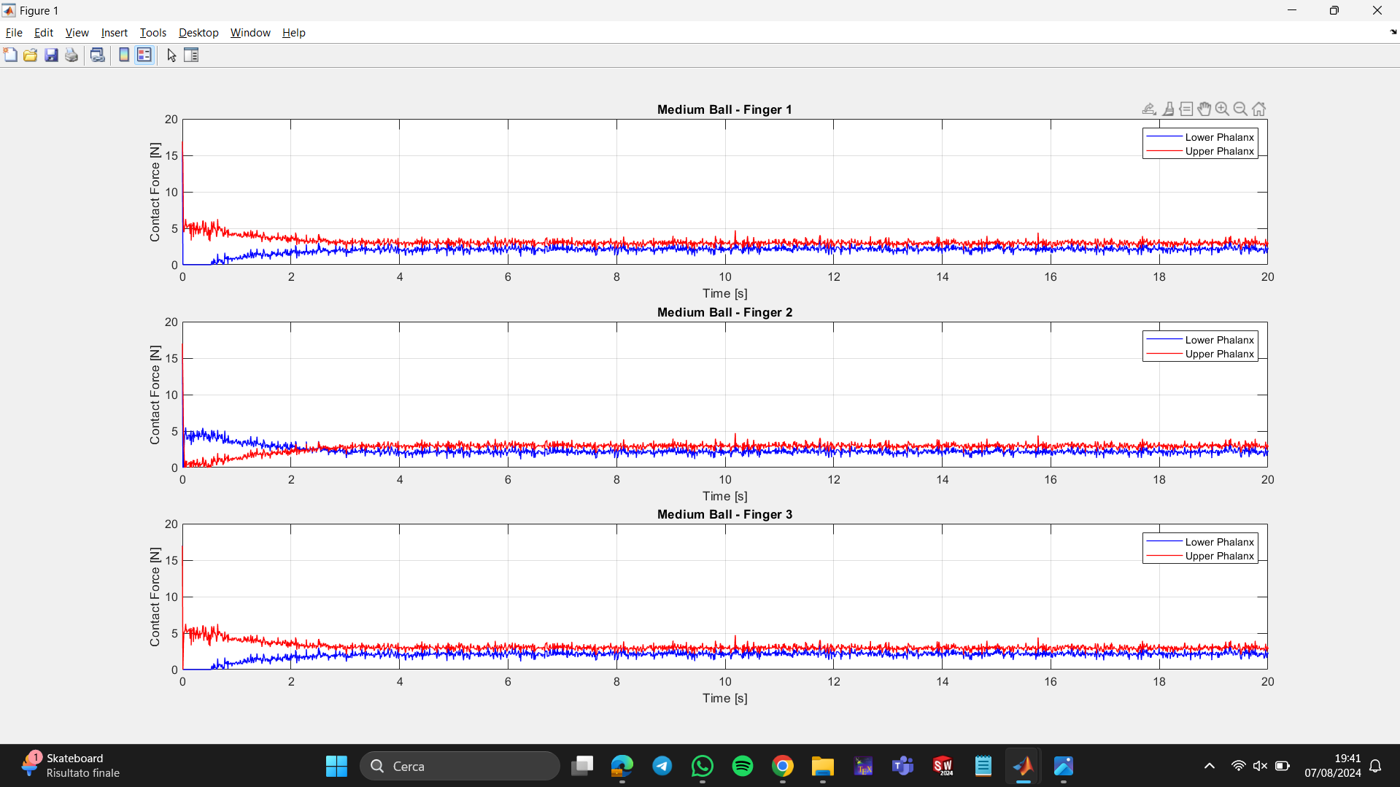
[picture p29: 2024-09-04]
for_simulation/large_ball/MATLAB/figures_forces_adaptive/figure_contact_force.png

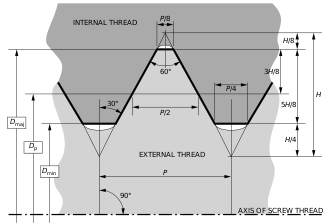
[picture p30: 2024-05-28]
medias/utilities/M3.png

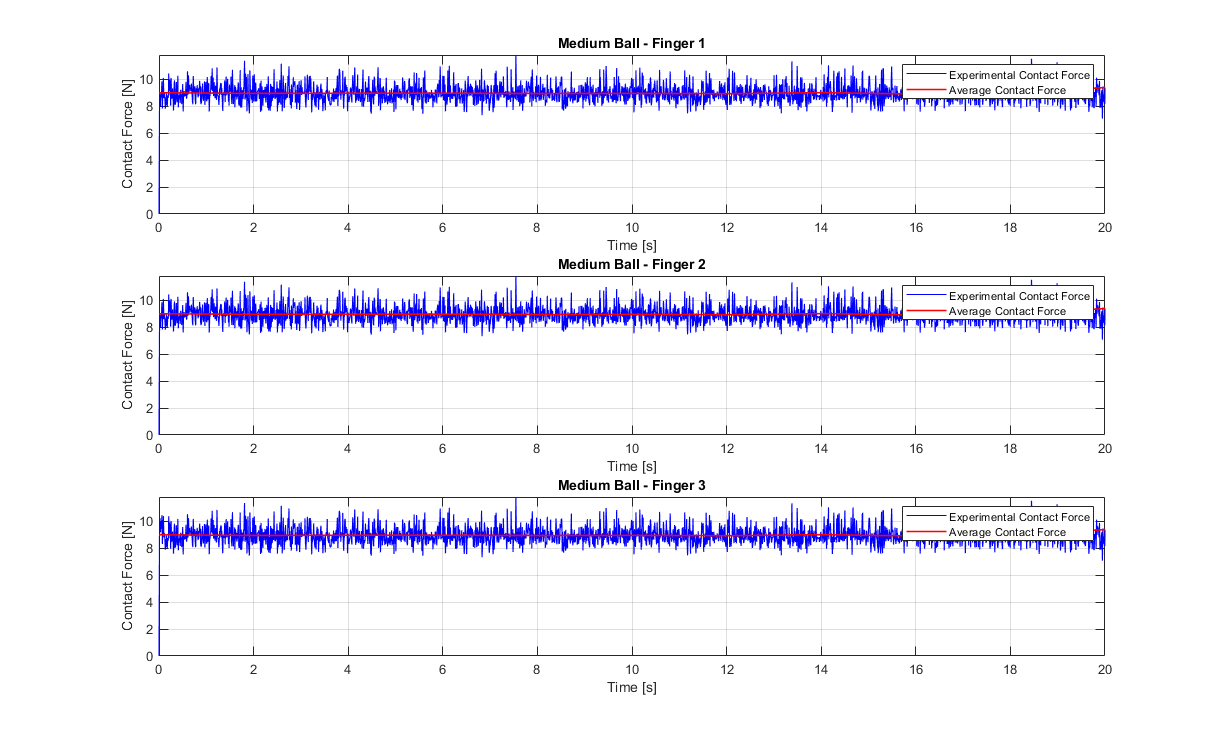
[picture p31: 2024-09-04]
for_simulation/medium_ball/MATLAB/figure_forces_parallel/figure_both_forces_parallel.png

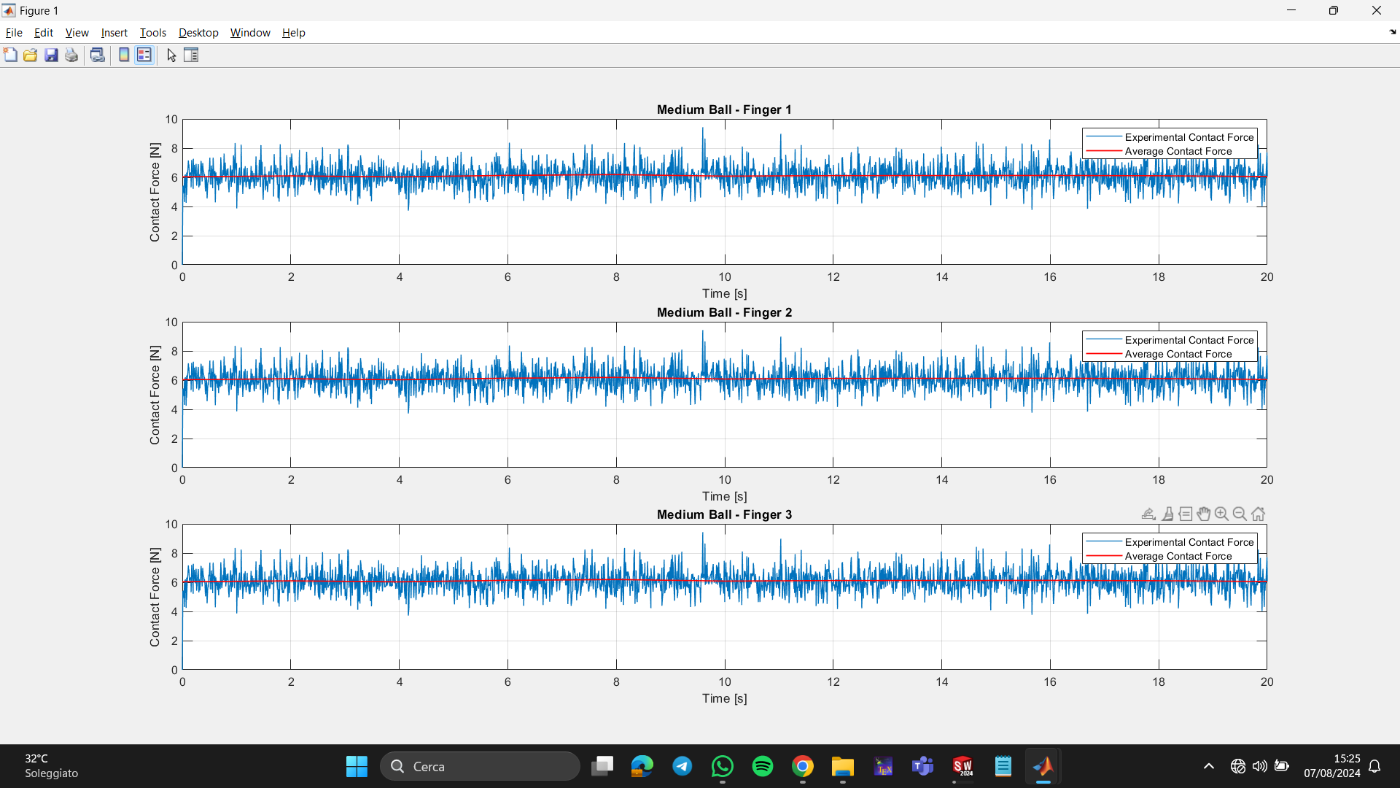
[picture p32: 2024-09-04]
for_simulation/large_ball/MATLAB/figure_forces_parallel/figure_both_forces_parallel.png

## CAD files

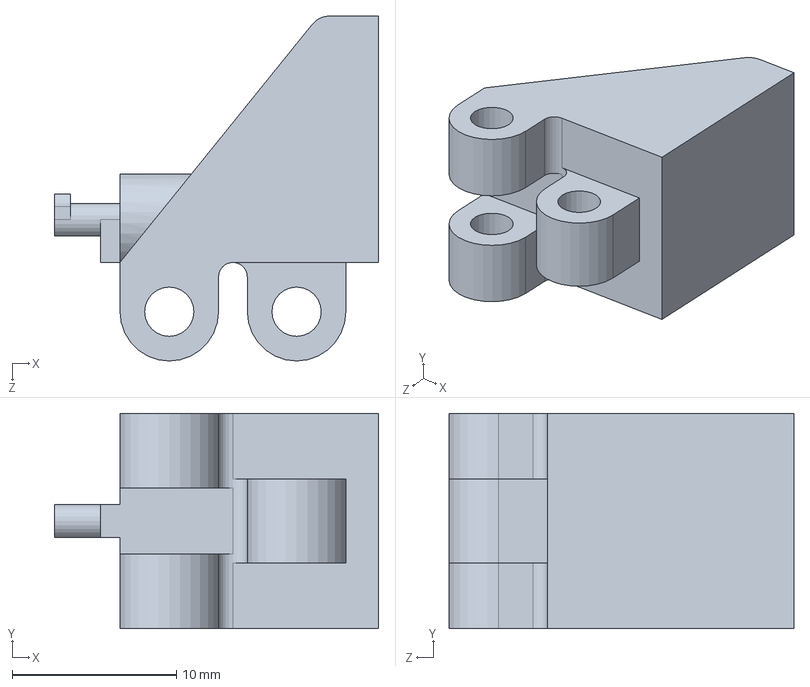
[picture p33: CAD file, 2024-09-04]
Endeffector_adaptive_config-3f_1gdl/final_gripper_2.SLDPRT
19.8 x 13.1 x 21.0 mm

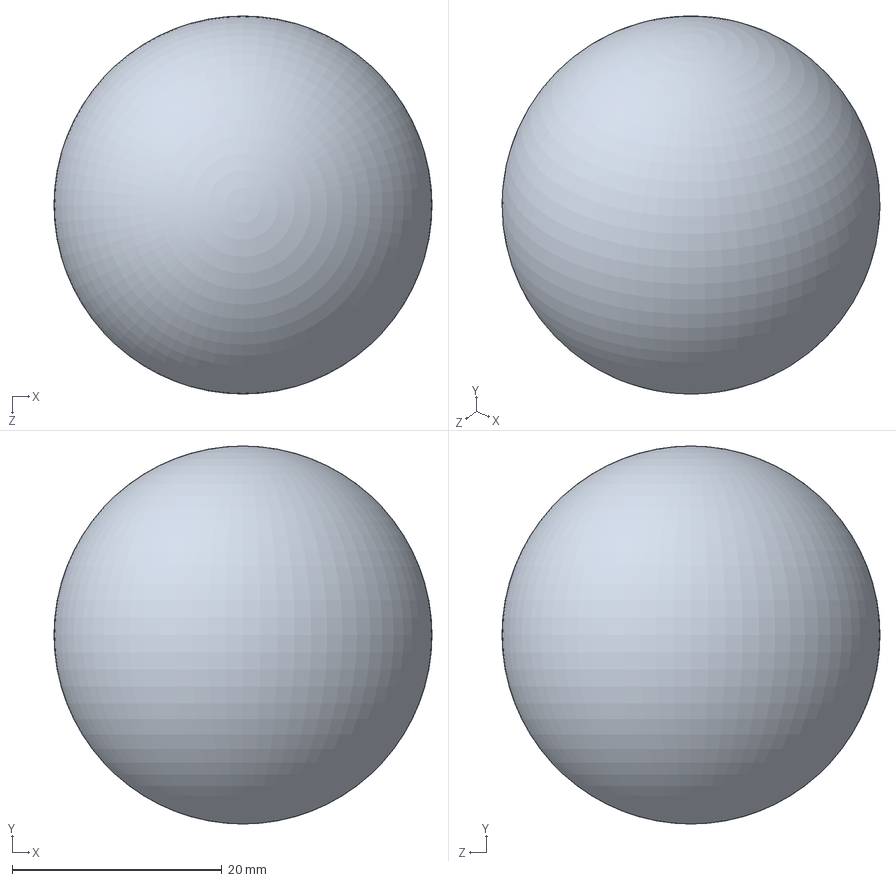
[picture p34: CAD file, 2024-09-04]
for_simulation/large_ball/large_ball.SLDPRT
36.0 x 36.0 x 36.0 mm

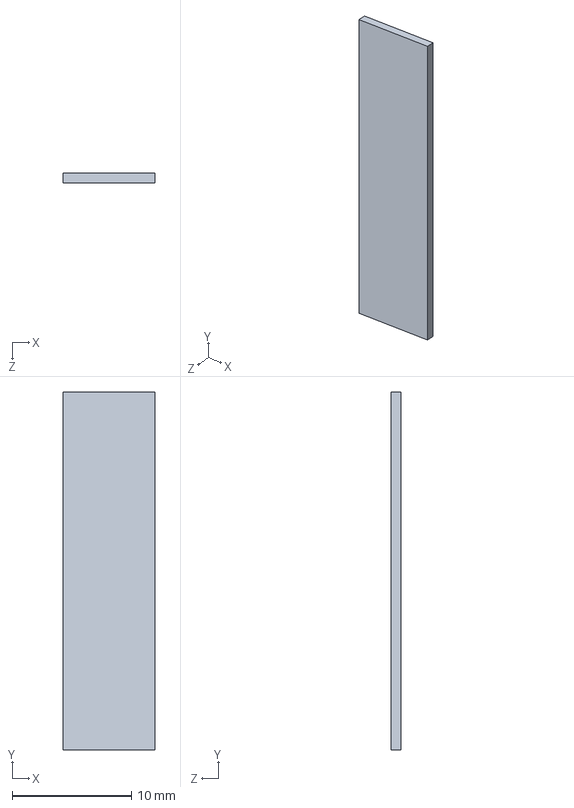
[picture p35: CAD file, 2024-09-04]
for_simulation/medium_ball/gommino_parallelo.SLDPRT
7.70 x 30.0 x 0.8 mm

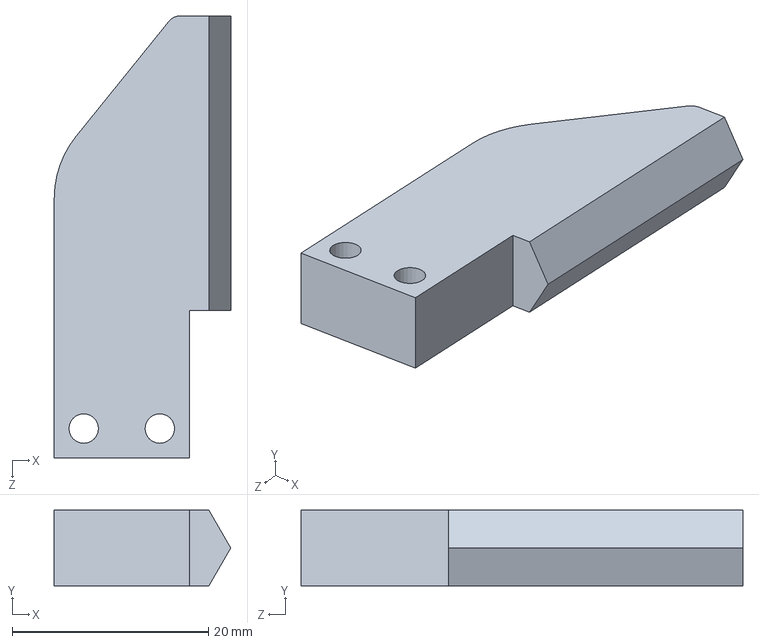
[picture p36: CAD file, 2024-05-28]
Other _endeffector_configurations/Endeffector_adaptive_config-3f_2gd/Gripper1_part - Copy.SLDPRT
18.0 x 7.70 x 45.0 mm

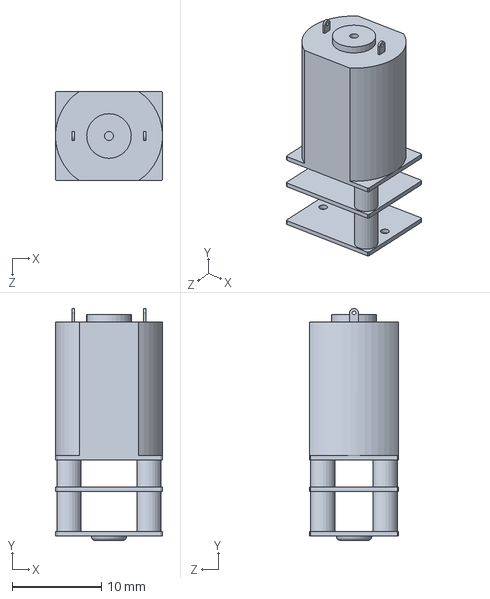
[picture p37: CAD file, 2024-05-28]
Other _endeffector_configurations/Endeffector_static_config-4f/DC_motor_part.SLDPRT
12.0 x 26.0 x 10.0 mm

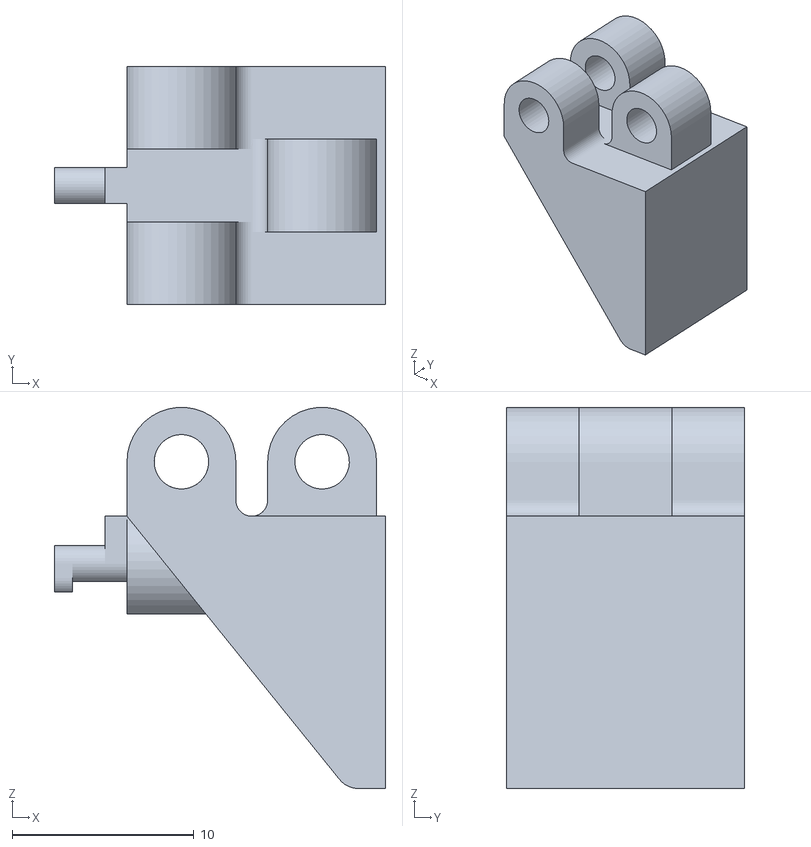
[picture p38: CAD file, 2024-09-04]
printable_parts/adaptive_endeffector/final_gripper.STL
18.2 x 13.1 x 21.0

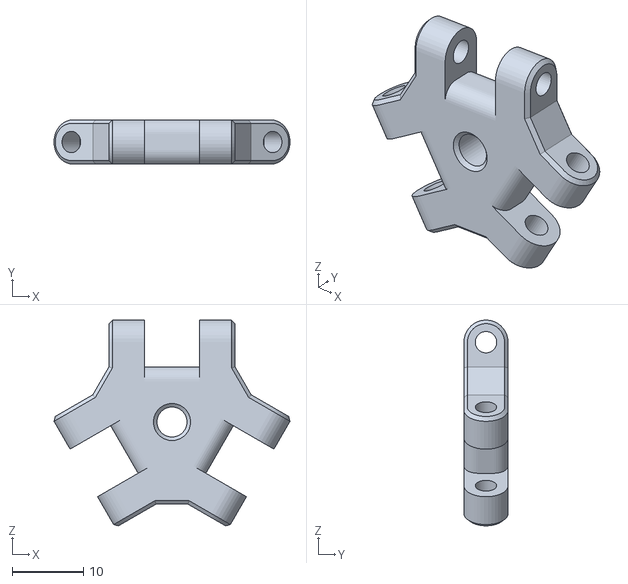
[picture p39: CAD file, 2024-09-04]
printable_parts/parallel_endeffector/Elevetor_part.STL
33.1 x 6.20 x 28.8

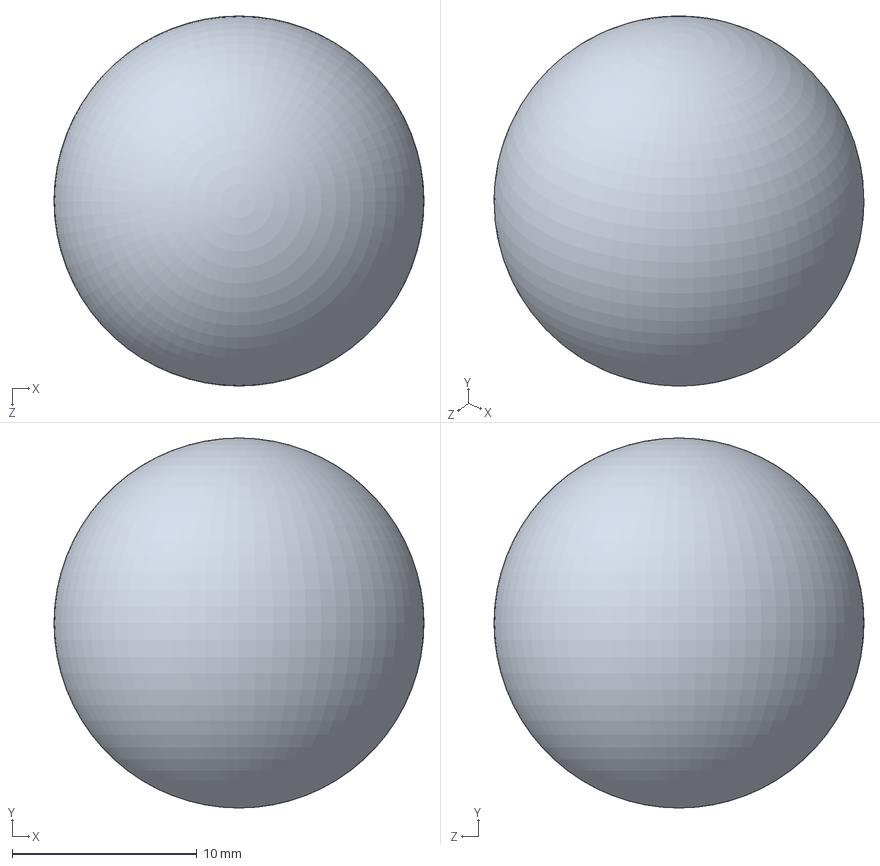
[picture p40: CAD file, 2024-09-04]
for_simulation/medium_ball/medium_ball.SLDPRT
20.0 x 20.0 x 20.0 mm

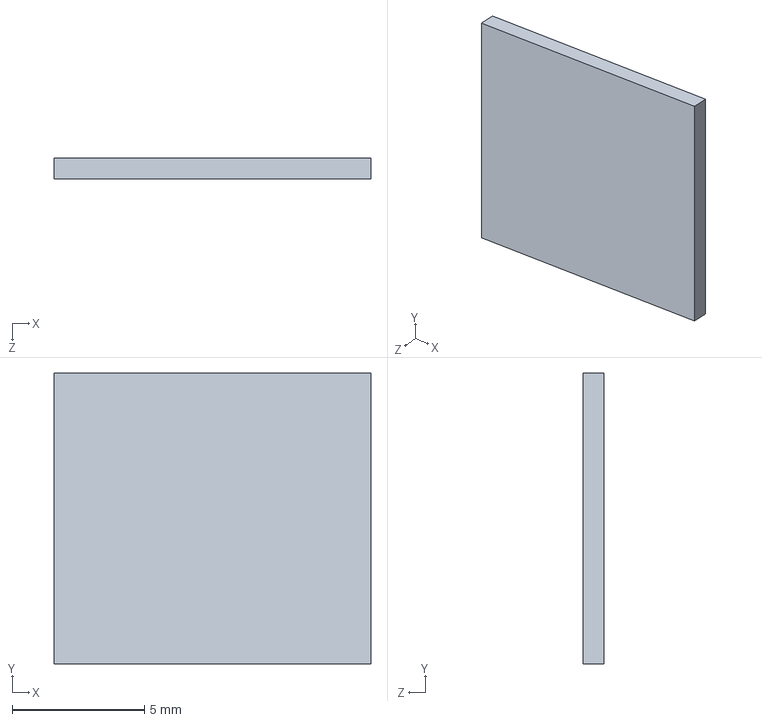
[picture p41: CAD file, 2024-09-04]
for_simulation/small_ball/gommino.SLDPRT
12.0 x 11.0 x 0.8 mm

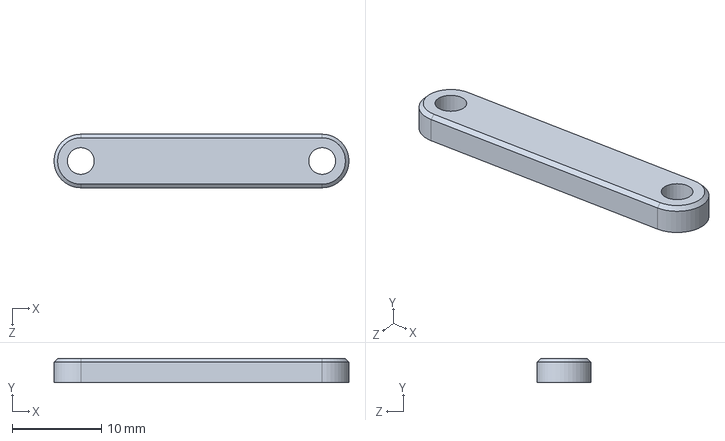
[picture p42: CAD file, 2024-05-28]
Other _endeffector_configurations/Endeffector_adaptive_config-3f_2gd/Connecting_rod_2_part.SLDPRT
33.0 x 2.70 x 6.00 mm

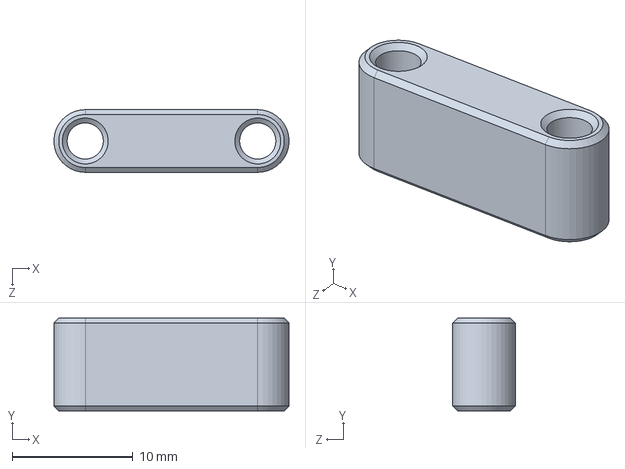
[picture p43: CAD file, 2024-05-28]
Other _endeffector_configurations/Endeffector_static_config-4f/Connecting_rod_1_part.SLDPRT
19.5 x 7.70 x 5.20 mm

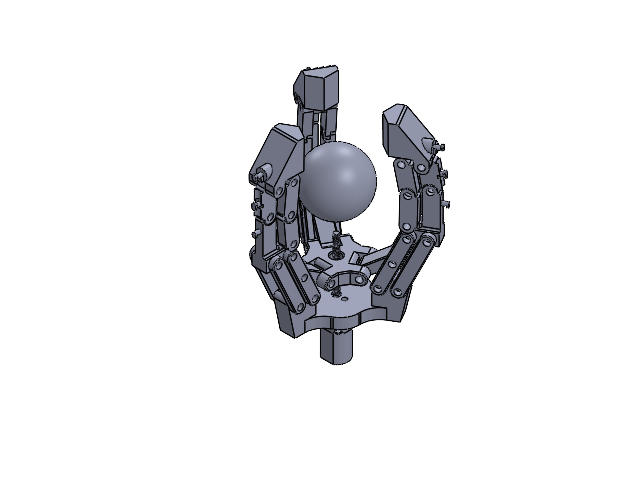
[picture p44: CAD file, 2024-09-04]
Other _endeffector_configurations/Endeffector_adaptive_config-3f/total.SLDASM
Base_part
Elevetor_part
Connecting_rod_3_part x 6
Connecting_rod_2_part x 6
Connecting_rod_1_part x 3
DC_motor_part
Shaft_part
final_gripper x 3
support_gripper x 3
rod_gripper_external x 3
rod_gripper_internal x 12
ball

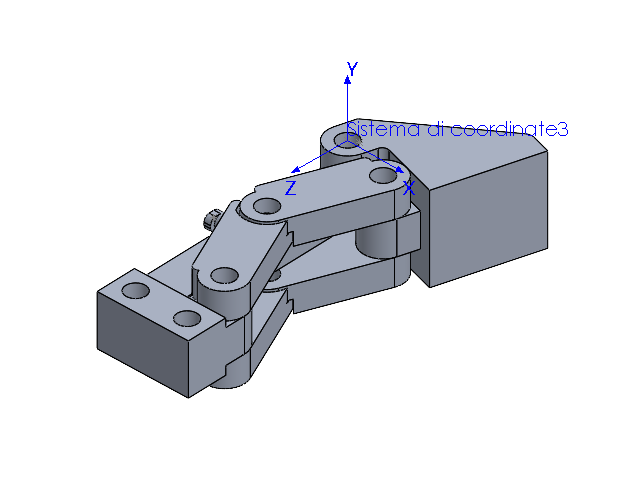
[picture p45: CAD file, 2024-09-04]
Endeffector_adaptive_config-3f_1gdl/dito_assemblato.SLDASM
final_gripper_2
support_gripper1
rod_gripper_internal x 4

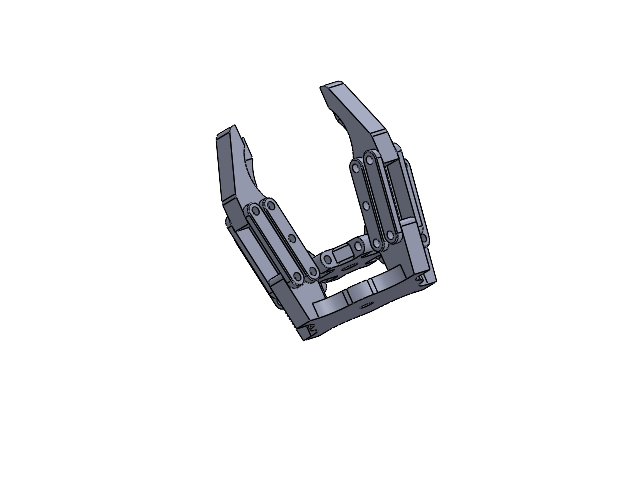
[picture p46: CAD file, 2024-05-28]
Other _endeffector_configurations/Endeffector_static_config-4f/total.SLDASM
Elevetor_part
Gripper1_part x 4
Connecting_rod_2_part x 8
Connecting_rod_3_part x 8
Connecting_rod_1_part x 4
Base_part

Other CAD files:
Other _endeffector_configurations/Endeffector_adaptive_config-3f_2gd/finger_assembly.SLDASM
for_simulation/small_ball/small_ball.SLDPRT
for_simulation/large_ball/gommino_parallelo.SLDPRT
Endeffector_adaptive_config-3f_1gdl/ball.SLDPRT
Endeffector_adaptive_config-3f_1gdl/rod_gripper_internal.SLDPRT
Endeffector_adaptive_config-3f_1gdl/support_gripper1.SLDPRT
Endeffector_static_config-3f/Gripper1_part.SLDPRT
Endeffector_static_config-3f/total.SLDASM
Other _endeffector_configurations/Endeffector_adaptive_config-3f_2gd/Base_part.SLDPRT
Other _endeffector_configurations/Endeffector_adaptive_config-3f_2gd/Connecting_rod_1_part.SLDPRT
Other _endeffector_configurations/Endeffector_adaptive_config-3f_2gd/Connecting_rod_3_part.SLDPRT
Other _endeffector_configurations/Endeffector_adaptive_config-3f_2gd/Elevetor_part.SLDPRT
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

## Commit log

2024-03-22 Endeffectors_3f parts
    [Part1.SLDPRT, Part2.SLDPRT, Part3.SLDPRT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]
2024-05-28 Squashed commit of the following:
    commit 044d7cc911729dbe30ae41854012be973fd5ddd4
    Author: Francesco8501 <stasi.fr0108@gmail.com>
    Date: Tue May 28 18:42:21 2024 +0200
    fix some problems
    commit 11ade330b099908a31fe8a6d0b23cd6547be17e0
    Author: FraGit2023 <dichiofrancesco734@gmail.com>
    Date: Thu May 23 14:15:54 2024 +0200
    new animations and plots
    commit 1d41a424e9c3f48498d162316bcc6612242e83b1
    Author: FraGit2023 <dichiofrancesco734@gmail.com>
    Date: Wed May 22 20:54:19 2024 +0200
    grafici forza di contatto
    commit d02a31c2a024e5fdebcf9c25c7e102cdb5ca69a3
    Author: FraGit2023 <dichiofrancesco734@gmail.com>
    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
    [13mm_gear_link.SLDPRT, 30mm_gear_4mm.SLDPRT, Base_part.SLDPRT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]
2024-09-04 update branch
    [13mm_gear_link.SLDPRT, 30mm_gear_4mm.SLDPRT, Base_part.SLDPRT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]

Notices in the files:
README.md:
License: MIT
